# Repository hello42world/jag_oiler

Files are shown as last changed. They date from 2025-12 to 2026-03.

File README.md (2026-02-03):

<table align="center">
	<tr>
		<td align="center" valign="top">
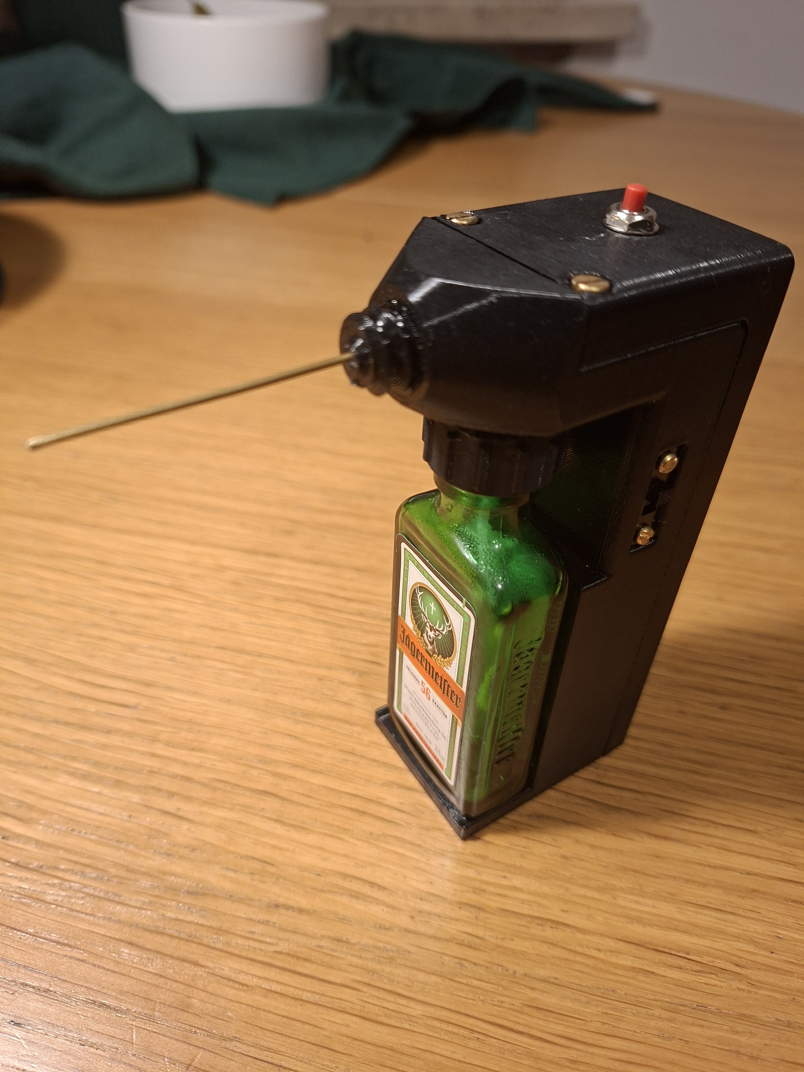
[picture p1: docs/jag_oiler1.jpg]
Jag Oiler Photo
			
		</td>
		<td align="center" valign="top">
			<a href="docs/jag_oiler.gif">Jag Oiler GIF</a><br>
			<a href="docs/jag_oiler_zoom.gif">Jag Oiler Zoom GIF</a>
		</td>
	</tr>
</table>

# What is it?

A ritual device for oiling your favorite bicycle's chain. This is an oil dispenser that uses a small peristaltic pump to administer small amounts of oil to lubricate your bicycle chain. It can work for other things too. The idea is to deliver a very small and even amount of thick oil precisely into the gap between the chain links. This way it gets sucked into the space between the links, leaving the surface of the chain mostly dry. Every push of the button dispenses about 0.005 ml of oil (can be adjusted).

# Why did you make it?

I was doing the chain clean/lubricate routine on my bicycles and got a bit frustrated by the fact that I could not squeeze an equal and small enough amount of oil onto every chain link every time.

# What? How is this better than an eyedropper/chain lube bottle?

An eyedropper is surely simpler, cheaper, and more reliable, so this gadget is mostly for people who like gadgets :) That said, IMO this device works better for dispensing small and even amounts, at least in my hands. 

# What oil to use

I found that thicker stuff works best. I use 80W-90 gear oil. If you put the right and small amount onto the link connection point, it gets sucked in and stays there, leaving the chain surface clean. See the video.

# What makes it special?

It uses a Jägermeister bottle as the oil container!

# How to build

See the [build guide](docs/how_to_build.md) for hints and bill of materials.

# Extra
Since most parts are sold in bulks I had enough of them to build a couple extra gadgets which I put on Tindie, in case there is anyone who wants one but doesn't want to build.

https://www.tindie.com/products/mediocregadgets/jag-oiler/

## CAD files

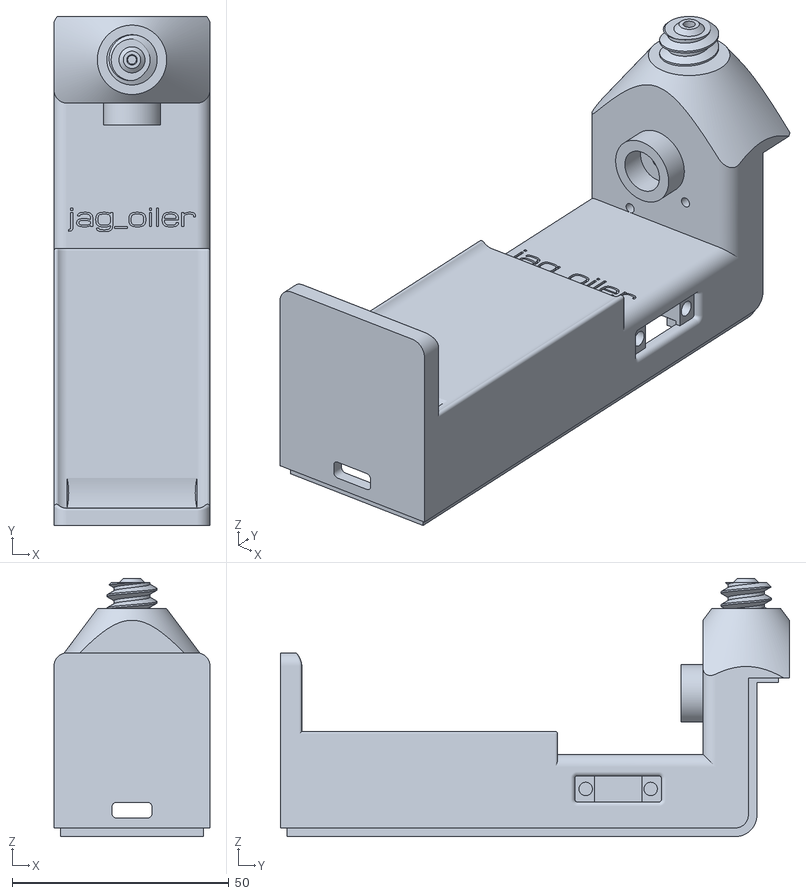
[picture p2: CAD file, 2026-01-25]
stl/jo_main.stl
36.0 x 117.5 x 59.6

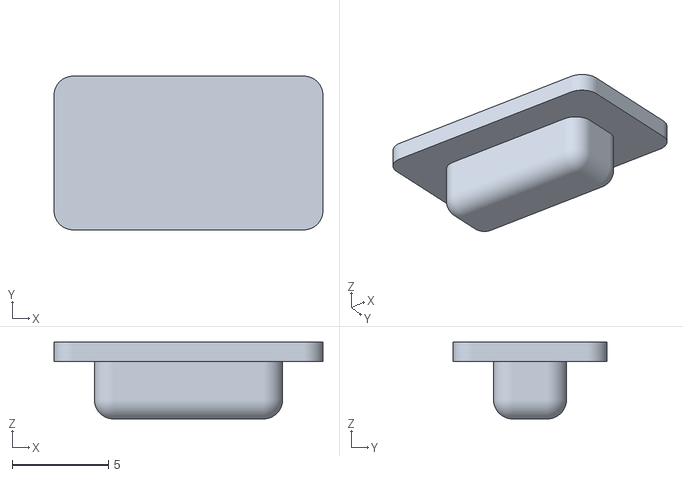
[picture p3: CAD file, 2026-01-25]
stl/jo_charge_indicator.stl
14.0 x 8.00 x 4.00

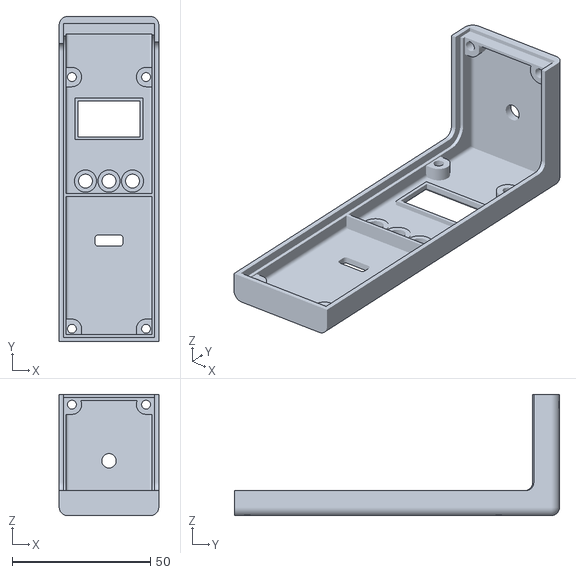
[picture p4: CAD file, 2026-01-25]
stl/jo_cover.stl
36.0 x 117.5 x 43.8

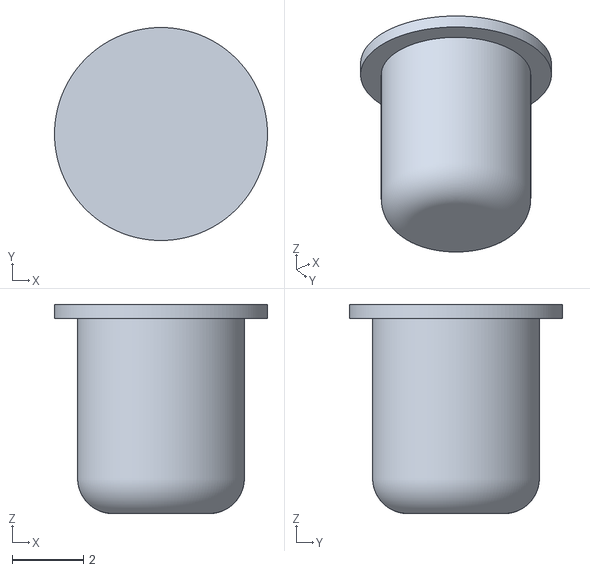
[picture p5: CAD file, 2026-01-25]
stl/jo_button.stl
6.00 x 6.00 x 5.90

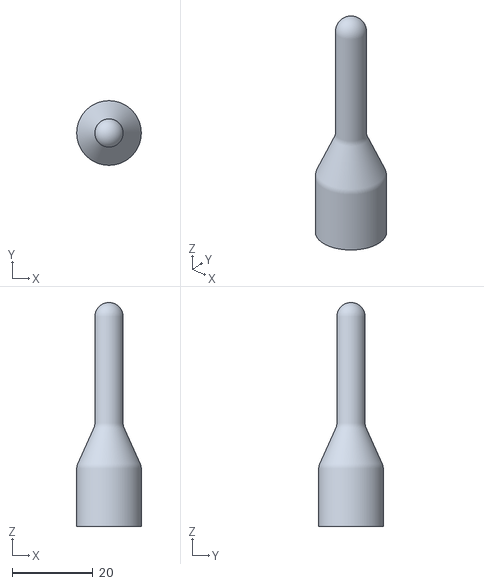
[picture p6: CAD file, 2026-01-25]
stl/jo_nozzle_cap.stl
16.0 x 16.0 x 55.5

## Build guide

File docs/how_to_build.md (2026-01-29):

# Build notes

The electronics part is a bunch of readymade modules from AliExpress hand-soldered to a custom PCB.
The only challenging part is probably the pump JST connector at the top with 1 mm spacing between the pins.
I'm not an electronics engineer, keep that in mind if you look at the schematics/PCB files.

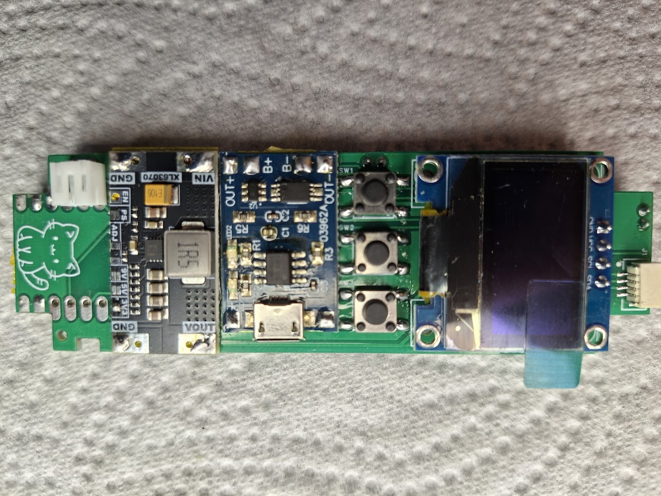
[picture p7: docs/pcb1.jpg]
PCB Front


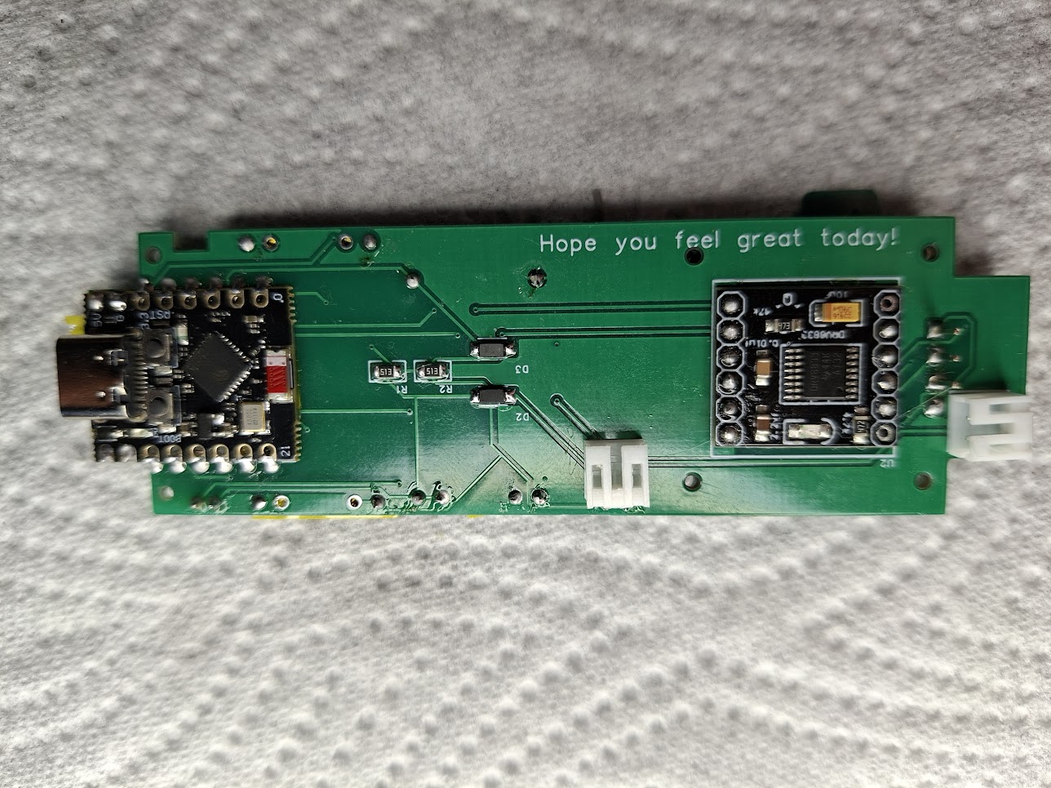
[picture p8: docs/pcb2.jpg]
PCB Back


The STL files for the case are also in this repo. I used PETG to print it.

# Bill of Materials

| Part | Details/AliExpress Search Term |
|---|---|
| ESP32-C3 Mini | |
| Pump | Tiny 8mm water pump stepper motor metering precision peristaltic flow control water liquid pump for medical experiment. |
| XL6309 | |
| TP4056 | |
| DRV8833 | Make sure it is enabled by default. There are 2 pads on the back side that should be shorted. |
| SSD1306 | There are 2 models: "original" and "new". You need the original one. |
| 14500 Li-Ion Battery x2 | |
| Filament | |
| PCB | |
| Diode | 1N5819 SOD-123 |
| Resistor 51kΩ x2 | 0805 51kΩ |
| Power Connector | JST PH 2.0 |
| Pump Connector | JST SH1.0 Connector 2P |
| Inserts 2mm x2 (Power Switch) | M2 (OD 3.5mm) |
| Inserts 3mm x6 (Cover) | M3×5.7 OD 4.6 |
| Bolts 2mm x2 | M2×3 |
| Bolts 3mm x6 | M3×12 |
| Screws x6 | M1.2, 5mm |
| Buttons SMT x3 | Micro 6×6×5mm momentary tactile push button switch 4-pin ON/OFF keys button. |
| Button Top | 5mm spring return momentary micro push button switch 0.5A 125VAC DS-402. |
| Power Switch | 50V 0.3A SS12F15 mini size black SPDT slide switch for DIY power electronic projects G6 1P2T toggle switch, handle 6mm, handle length 2mm. |
| PTFE Tube | ID 1mm, OD 2mm |
| Brass Tube | OD 1.2mm, ID 0.8mm |
| Jägermeister Bottle | 20ml |

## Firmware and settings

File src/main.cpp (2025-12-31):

#include <Arduino.h>
#include <Wire.h>
#include <Adafruit_GFX.h>
#include <Adafruit_SSD1306.h>

#include "app.h"


App* app = nullptr;

void setup() {
  // WiFi.mode(WIFI_OFF);

  // Initialize serial communication
  Serial.begin(115200); 

  app = new App();
}

void mui_loop(void);


void loop() {
  app->loop();
}

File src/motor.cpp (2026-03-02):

#include "motor.h" 
#include "motor_events.h"

#define PIN_AIN1 5
#define PIN_AIN2 6
#define PIN_BIN1 7
#define PIN_BIN2 10

const int progressStep = 10;

Motor::Motor(EventBus* eventBus) 
  : stepper_(AccelStepper::FULL4WIRE, PIN_AIN1, PIN_AIN2, PIN_BIN1, PIN_BIN2) 
  , eventBus_(eventBus)
  , lastState_(IDLE)
{
  
  stepper_.setMaxSpeed(1500);    
  stepper_.setAcceleration(25000);  
  stepper_.setCurrentPosition(0);
  stepper_.disableOutputs();
}

void Motor::beginPortion(int32_t steps) {
  if (getState() == RUNNING_PORTION) {
    return;
  }
  stepper_.enableOutputs();
  stepper_.move(steps);
  eventBus_->publish(std::make_unique<MotorProgressEvent>(0, steps > 0));
  lastProgress_ = 0;
}

void Motor::loop() {
  stepper_.run();
  
  if (getState() != lastState_) {
    if (getState() == IDLE) {
      stepper_.disableOutputs();
      stepper_.setCurrentPosition(0);
      eventBus_->publish(std::make_unique<MotorProgressEvent>(100, false));
    }
  }

  if (getState() == RUNNING_PORTION) {
    auto progress = getPortionProgress();
    if (progress / progressStep != lastProgress_ / progressStep) {
      lastProgress_ = progress;
      eventBus_->publish(std::make_unique<MotorProgressEvent>(progress, stepper_.targetPosition() > 0));
    }
  }

  lastState_ = getState();
}

bool Motor::handleEvent(const Event* event) {
  if (event->id == EventID::MotorStartCommand) {
    const MotorStartCommandEvent* motorEvent = static_cast<const MotorStartCommandEvent*>(event);
    beginPortion(motorEvent->stepsToMove);
  } else if (event->id == EventID::MotorStopCommand) {
    stepper_.stop();
    eventBus_->publish(std::make_unique<MotorProgressEvent>(100, false));
  } else {
    return false;
  }
  return true;
}

int16_t Motor::getPortionProgress() const {
  if (getState() == IDLE) {
    return 100;
  }
  AccelStepper& stepper = const_cast<AccelStepper&>(stepper_);
  int16_t totalSteps = abs(stepper.targetPosition());
  int16_t remainingSteps = abs(stepper.distanceToGo());
  return (totalSteps - remainingSteps) * 100 / totalSteps;
}

Motor::State Motor::getState() const {
  return const_cast<AccelStepper&>(stepper_).isRunning() ? RUNNING_PORTION : IDLE;
}

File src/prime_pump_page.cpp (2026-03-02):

#include "prime_pump_page.h"
#include "ui/events.h"
#include "ui/xmui.h"
#include "motor.h"
#include "motor_events.h"

PrimePumpPage::PrimePumpPage(PageManager* pageManager)
  : Page(pageManager)
  , state_(State::Ready)
  , buttonHint_(pageManager->u8g2(), "Flush", "Stop", "Prime")
{
}

bool PrimePumpPage::handleEvent(const Event* event) {
  if (event->id == EventID::FullRedraw) {
    draw();
  } else if (event->id == EventID::Button) {
    const ui::ButtonEvent* buttonEvent = static_cast<const ui::ButtonEvent*>(event);
    if (buttonEvent->button == U8X8_MSG_GPIO_MENU_SELECT) {
      publishEvent(std::make_unique<MotorStopCommandEvent>());
    } else if (buttonEvent->button == U8X8_MSG_GPIO_MENU_HOME) {
      publishEvent(std::make_unique<MotorStopCommandEvent>());
      publishEvent(std::make_unique<PageClosedEvent>(this));
    } else if (buttonEvent->button == U8X8_MSG_GPIO_MENU_NEXT) {
      publishEvent(std::make_unique<MotorStartCommandEvent>(Motor::TURN_STEPS * 20));
    } else if (buttonEvent->button == U8X8_MSG_GPIO_MENU_PREV) {
      publishEvent(std::make_unique<MotorStartCommandEvent>(-Motor::TURN_STEPS * 20));
    }
  } else if (event->id == EventID::MotorProgress && pageManager_->isActive(this)) {
    auto progressEvt = static_cast<const MotorProgressEvent*>(event);
    if (progressEvt->progressPercent == 0) {
      state_ = progressEvt->forward ? State::Priming : State::Flushing;
      publishEvent(std::make_unique<ui::FullRedrawEvent>());
    } else if (progressEvt->progressPercent == 100) {
      state_ = State::Ready;
      publishEvent(std::make_unique<ui::FullRedrawEvent>());
    }
  } else {
    return false;
  }
  return true;
}


void PrimePumpPage::draw() {
  if (state_ == State::Ready) {
    printInCenter("Ready");
  } else if (state_ == State::Priming) {
    printInCenter("Priming...");
  } else if (state_ == State::Flushing) {
    printInCenter("Flushing...");
  }
  buttonHint_.draw();
}

void PrimePumpPage::printInCenter(const char* str) {
  pageManager_->u8g2()->setFont(XMUI_BIG_FONT);
  u8g2_uint_t x = (pageManager_->u8g2()->getWidth() - pageManager_->u8g2()->getStrWidth(str)) / 2;
  pageManager_->u8g2()->drawStr(x, (pageManager_->u8g2()->getHeight() + 10) / 2, str);
}

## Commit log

2025-10-12 dummy progressbar
    [cap.scad, threads.scad]
2025-10-12 clean up
    [cap.scad, threads.scad]
2025-11-16 Implemented simple app framework
2025-11-17 Motor turns, progress displayed
2025-11-20 Reworked event system a bit
    [app.cpp, dispense_page.cpp, menu_page.cpp]
2025-11-22 Added battery voltage measuring.
2025-11-22 Fixed battery voltage measurement.
    [battery.cpp, dispense_page.cpp]
2025-12-27 Adjusted pins for prototype
2025-12-28 Added button hints on pump flush page
2025-12-29 Added battery indicator
2025-12-30 Fixed message handling to check if page is active.
    [app.cpp, dispense_page.cpp, prime_pump_page.cpp]
2025-12-31 Removed millivolts display
2026-01-12 Fixed initial motor state.
    [motor.cpp]
2026-01-25 added stls and schematics
    [jo_button.stl, jo_charge_indicator.stl, jo_cover.stl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]
2026-01-25 Added pcb photos
